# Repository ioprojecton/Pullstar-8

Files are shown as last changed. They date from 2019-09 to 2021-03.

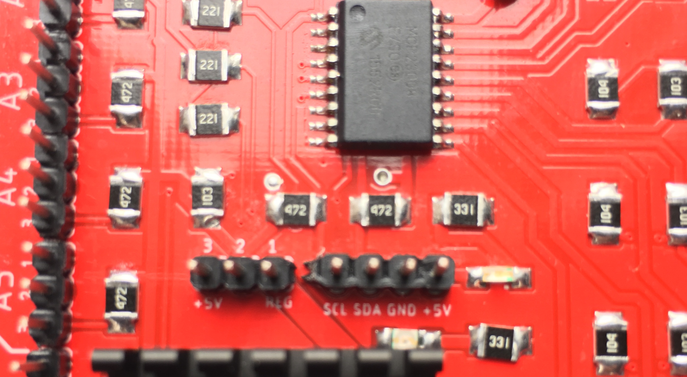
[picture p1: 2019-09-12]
IMG_7.JPG

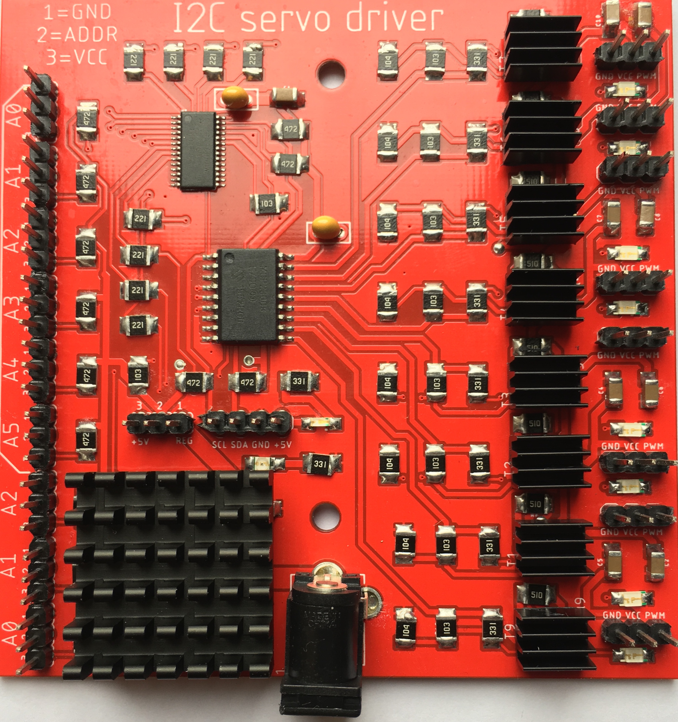
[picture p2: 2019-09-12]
IMG_5.JPG

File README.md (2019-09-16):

# Pullstar-8
I2C 8 Port Servo Driver

The I2C servo driver board by Surepic© is designed to make connecting motors, sensors and other components to your Arduino,Rasberi Pi-based project as fast and easy as possible.

This board allows your Raspberry Pi,Arduino, etc., to control up to 8 servo motors in a simple way via an I2C connection. Thanks to its I2C capabilities, this board saves the Raspberry Pi's,Arduino`s GPIO pins, allowing you to use them for other purposes.

Each of this board's 8 servo motor GPIO pin headers has been spaced out to the standard 3-pin servo pinout (ground, 5V, signal) to make it easier to attach your servo motors and can supply up to 1.25A to each of 8 outputs.

This driver includes headers to connect to a Raspberry Pi,Arduino , so there is no need for soldering to make it up and running.

Using the onboard jumpers for power selection, the input power can be supplied via Arduino's,Rasberi Pi`s regulated voltage, or a completely separate power supply attached to the board's 2.1mm barrel jack. This feature makes this board ideal if you are connecting multiple servos!

Compared to other servo drivers this board offers:
  Independant power control(ON/OFF) to each outputs via i2c.
  Independant duty cycle control to each outputs via i2c.
  Adjustible frequency to up to 1.6khz.
  1.25A per output when powered from external supply.
  LEDs on each output providing feedback if output is ON or OFF.
  2 selectible power sources selectible with jumpers and with led status indicators.
  Onboard voltage regulator (input 6-7v 3A recommended), when barrel jack is used.
  Open collector outputs on power pins.
  I2C addressess are selectable with jumpers for both onboard ics.
  Fully compatible with fast mode I2C 400kbits/s.
  Each board is fully tested before shipping.
  
=========================

Features:

•16 PWM channels, controllable over I2C
•2.1mm industry standard barrel jack port
•Contain an I2C-controlled PWM ic with a built-in clock
•12-bit resolution for each output - for servos(4us at 60hz)
•Controls up to 8 servos
.Dual power inputs (selectible with jumpers).
.Onboard low noise low ripple regulator.
.115 x 105mm size
.Feedback LEDs on each output
.Independant power control to each output

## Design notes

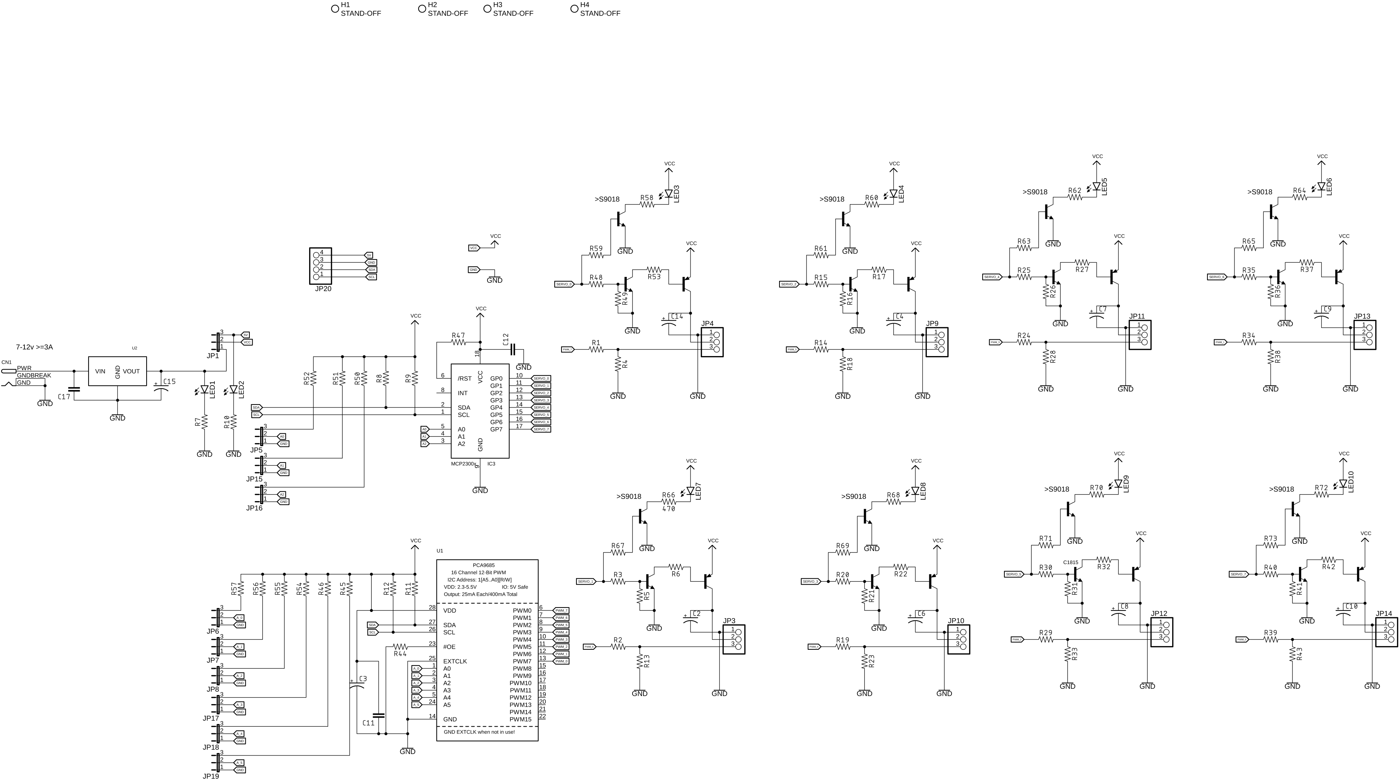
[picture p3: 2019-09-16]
Schematic.jpg

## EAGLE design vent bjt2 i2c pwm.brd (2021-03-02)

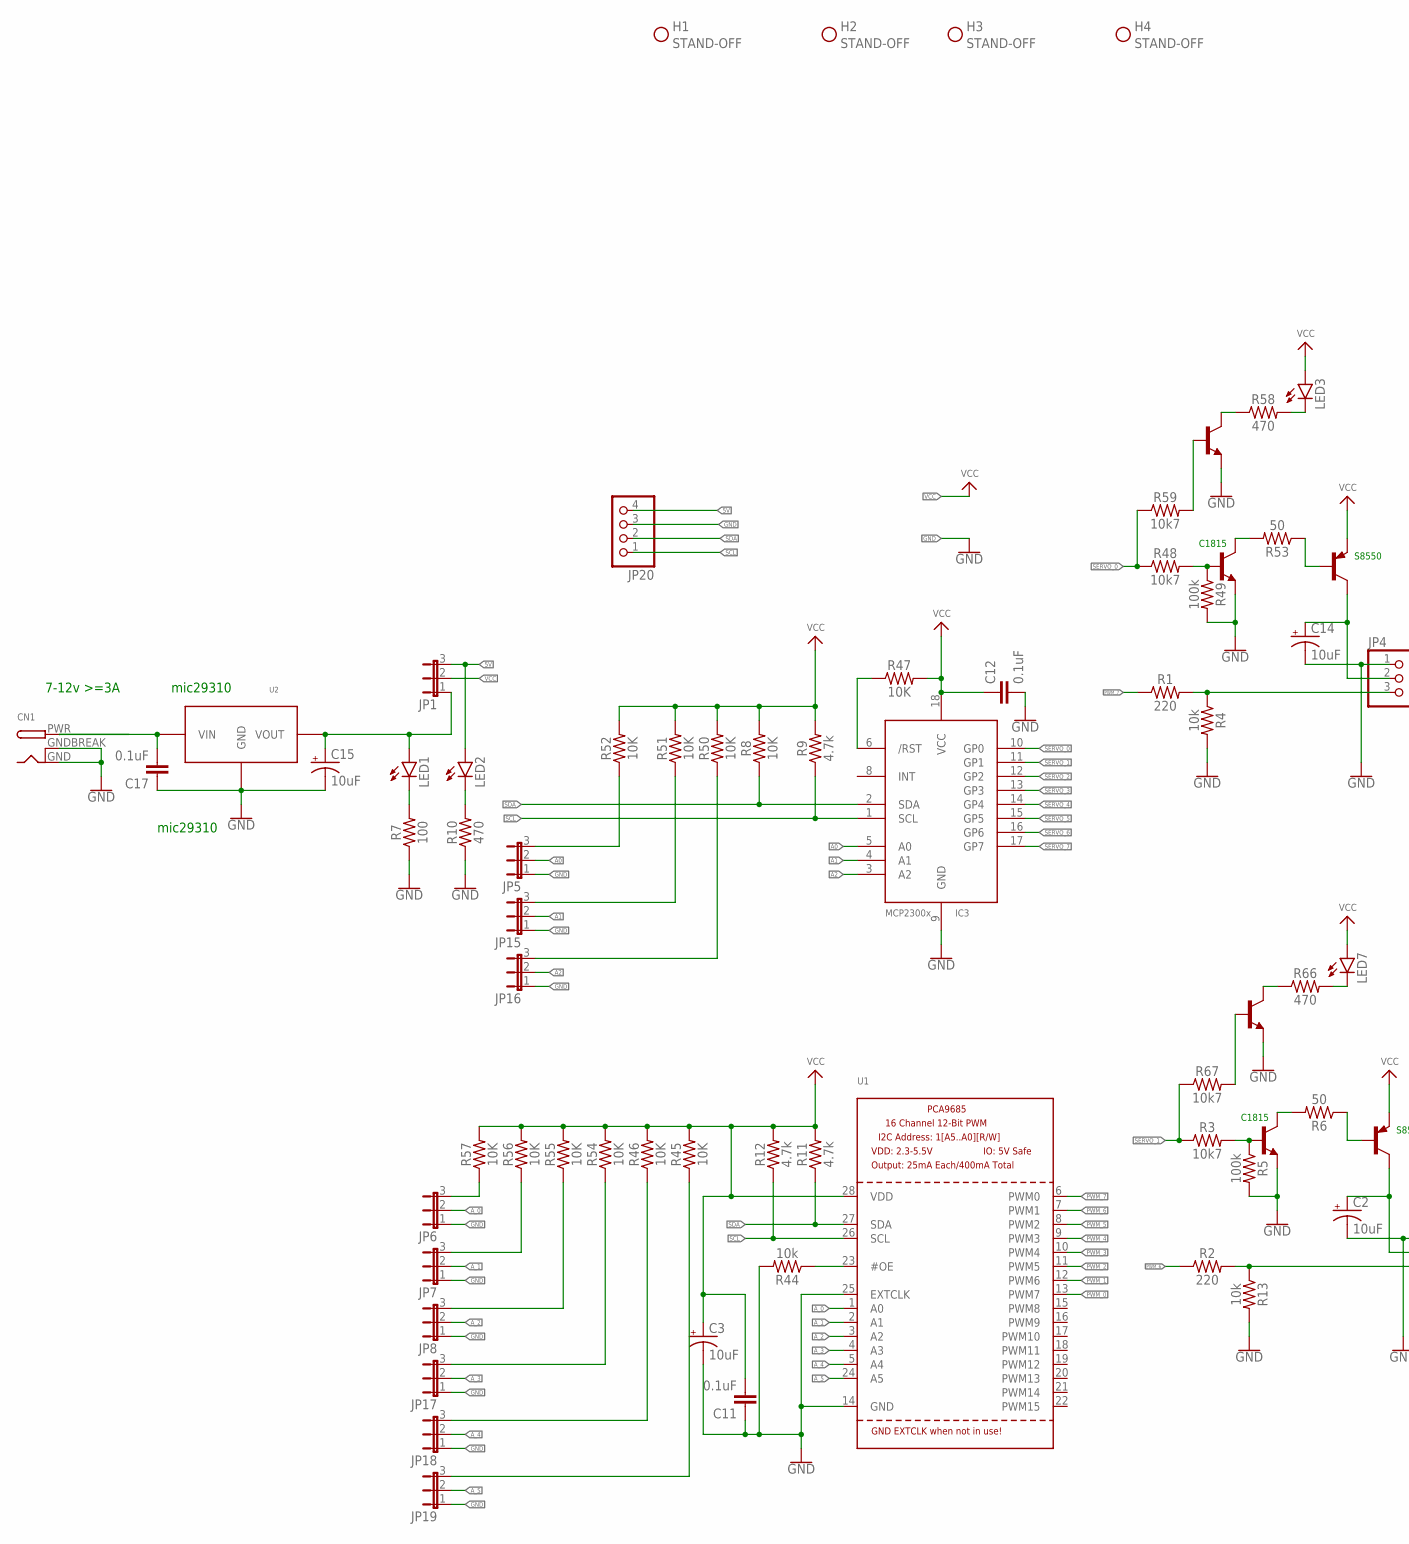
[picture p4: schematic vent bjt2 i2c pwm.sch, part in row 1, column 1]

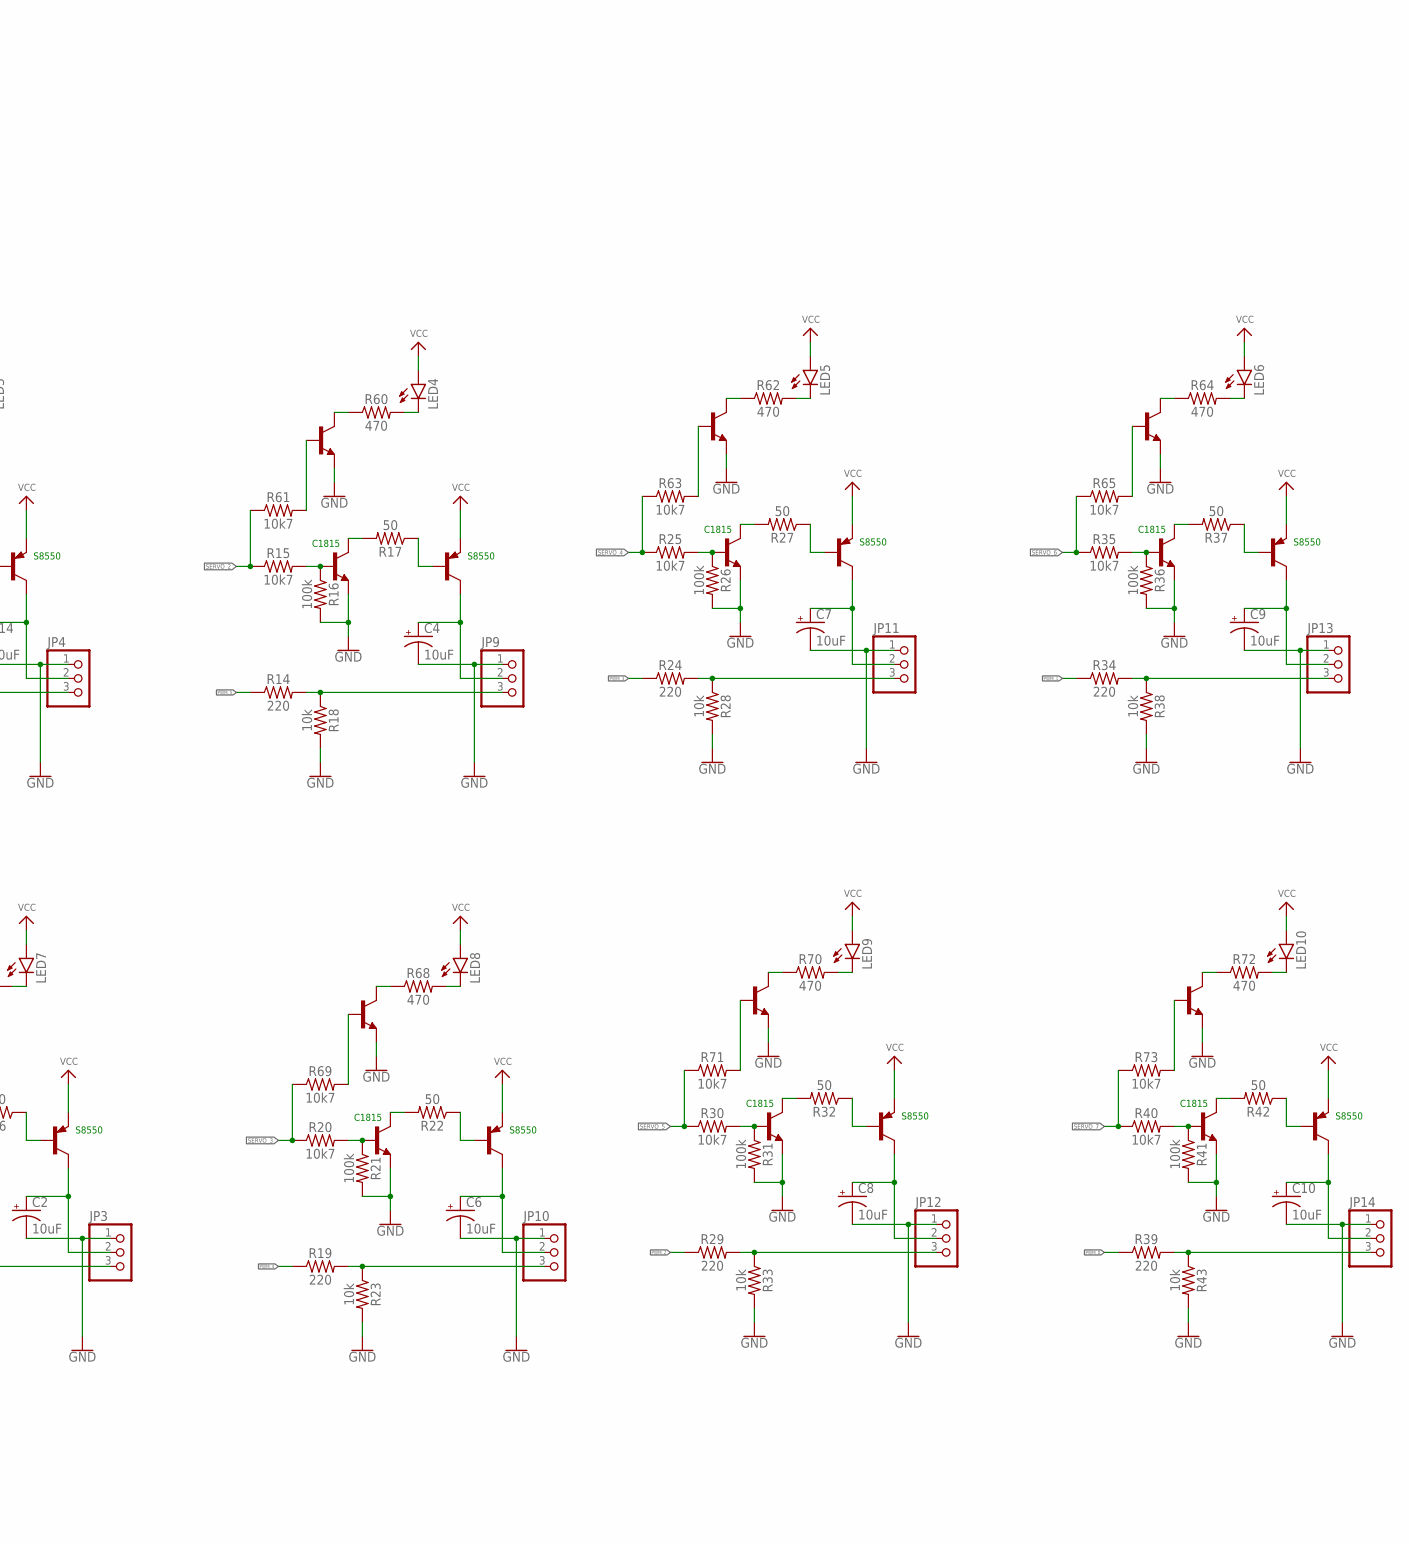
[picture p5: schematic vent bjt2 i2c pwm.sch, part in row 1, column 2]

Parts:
C2, C3, C4, C6, C7, C8, C9, C10, C14, C15: 10uF; CPOL-RADIAL-2.5MM-5MM
C11, C12, C17: 0.1uF; CAP-PTH-SMALL-KIT
CN1: DCBARRELPTH; DCJACK_2MM_PTH
H1, H2, H3, H4: STAND-OFF
IC3: MCP23008/P; DIL18
JP1, JP5, JP6, JP7, JP8, JP15, JP16, JP17, JP18, JP19: JP2E; JP2
JP3, JP4, JP9, JP10, JP11, JP12, JP13, JP14: PINHD-1X3; 1X03
JP20: PINHD-1X4; 1X04
LED1, LED2, LED3, LED4, LED5, LED6, LED7, LED8, LED9, LED10: LEDCHIPLED_1206; CHIPLED_1206
Q1, Q2, Q3, Q4, Q5, Q6, Q7, Q9: 2N2907; TO92-EBC-OVAL
R1, R2, R14, R19, R24, R29, R34, R39: 220; AXIAL-0.3
R3, R15, R20, R25, R30, R35, R40, R48, R59, R61, R63, R65, R67, R69, R71, R73: 10k7; AXIAL-0.3
R4, R13, R18, R23, R28, R33, R38, R43, R44: 10k; AXIAL-0.3
R5, R16, R21, R26, R31, R36, R41, R49: 100k; AXIAL-0.3
R6, R17, R22, R27, R32, R37, R42, R53: 50; AXIAL-0.3
R7: 100; AXIAL-0.3
R8, R45, R46, R47, R50, R51, R52, R54, R55, R56, R57: 10K; AXIAL-0.3
R9, R11, R12: 4.7k; AXIAL-0.3
R10, R58, R60, R62, R64, R66, R68, R70, R72: 470; AXIAL-0.3
T1, T2, T3, T4, T5, T6, T7, T9: 2SC1815; TO92-ECB
U1: PCA9685; TSSOP28
U2: MIC29310_TO-263; TO263-3
U3, U4, U5, U6, U7, U8, U9, U10: S9018; TO92-EBC

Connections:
5V: JP1.3, JP20.4, LED2.A
5V_REG: C15.1 (+), JP1.1, LED1.A, U2.3 (VOUT)
A0: IC3.5 (A0), JP5.2
A1: IC3.4 (A1), JP15.2
A2: IC3.3 (A2), JP16.2
A_0: JP6.2, U1.1 (A0)
A_1: JP7.2, U1.2 (A1)
A_2: JP8.2, U1.3 (A2)
A_3: JP17.2, U1.4 (A3)
A_4: JP18.2, U1.5 (A4)
A_5: JP19.2, U1.24 (A5)
GND: C2.2 (-), C3.2 (-), C4.2 (-), C6.2 (-), C7.2 (-), C8.2 (-), C9.2 (-), C10.2 (-), C11.1, C12.2, C14.2 (-), C15.2 (-), C17.1, CN1.GND, CN1.GNDBREAK, IC3.9 (GND), JP3.1, JP4.1, JP5.1, JP6.1, JP7.1, JP8.1, JP9.1, JP10.1, JP11.1, JP12.1, JP13.1, JP14.1, JP15.1, JP16.1, JP17.1, JP18.1, JP19.1, JP20.3, R4.P$2 (2), R5.P$2 (2), R7.P$1 (1), R10.P$1 (1), R13.P$2 (2), R16.P$2 (2), R18.P$2 (2), R21.P$2 (2), R23.P$2 (2), R26.P$2 (2), R28.P$2 (2), R31.P$2 (2), R33.P$2 (2), R36.P$2 (2), R38.P$2 (2), R41.P$2 (2), R43.P$2 (2), R44.P$2 (2), R49.P$2 (2), T1.E, T2.E, T3.E, T4.E, T5.E, T6.E, T7.E, T9.E, U1.14 (GND), U1.25 (EXTCLK), U2.2 (GND), U2.TAB (GND), U3.E, U4.E, U5.E, U6.E, U7.E, U8.E, U9.E, U10.E
unnamed: JP4.3, R1.P$2 (2), R4.P$1 (1)
unnamed: JP3.3, R2.P$2 (2), R13.P$1 (1)
unnamed: Q9.B, R53.P$1 (1)
unnamed: R3.P$2 (2), R5.P$1 (1), T1.B
unnamed: R6.P$2 (2), T1.C
unnamed: JP8.3, R55.P$1 (1)
unnamed: C2.1 (+), JP3.2, Q1.C
unnamed: C17.2, CN1.PWR, U2.1 (VIN)
unnamed: Q1.B, R6.P$1 (1)
unnamed: JP9.3, R14.P$2 (2), R18.P$1 (1)
unnamed: JP6.3, R57.P$1 (1)
unnamed: JP7.3, R56.P$1 (1)
unnamed: R44.P$1 (1), U1.23 (#OE)
unnamed: LED1.C, R7.P$2 (2)
unnamed: LED2.C, R10.P$2 (2)
unnamed: R58.P$1 (1), U3.C
unnamed: JP17.3, R54.P$1 (1)
unnamed: JP18.3, R46.P$1 (1)
unnamed: R15.P$2 (2), R16.P$1 (1), T2.B
unnamed: R17.P$2 (2), T2.C
unnamed: C4.1 (+), JP9.2, Q2.C
unnamed: Q2.B, R17.P$1 (1)
unnamed: JP10.3, R19.P$2 (2), R23.P$1 (1)
unnamed: R20.P$2 (2), R21.P$1 (1), T3.B
unnamed: R22.P$2 (2), T3.C
unnamed: C6.1 (+), JP10.2, Q3.C
unnamed: Q3.B, R22.P$1 (1)
unnamed: JP11.3, R24.P$2 (2), R28.P$1 (1)
unnamed: R25.P$2 (2), R26.P$1 (1), T4.B
unnamed: R27.P$2 (2), T4.C
unnamed: C7.1 (+), JP11.2, Q4.C
unnamed: Q4.B, R27.P$1 (1)
unnamed: JP12.3, R29.P$2 (2), R33.P$1 (1)
unnamed: R30.P$2 (2), R31.P$1 (1), T5.B
unnamed: R32.P$2 (2), T5.C
unnamed: C8.1 (+), JP12.2, Q5.C
unnamed: Q5.B, R32.P$1 (1)
unnamed: JP13.3, R34.P$2 (2), R38.P$1 (1)
unnamed: R35.P$2 (2), R36.P$1 (1), T6.B
unnamed: R37.P$2 (2), T6.C
unnamed: C9.1 (+), JP13.2, Q6.C
unnamed: Q6.B, R37.P$1 (1)
unnamed: JP19.3, R45.P$1 (1)
unnamed: JP5.3, R52.P$1 (1)
unnamed: JP15.3, R51.P$1 (1)
unnamed: JP16.3, R50.P$1 (1)
unnamed: IC3.6 (/RST), R47.P$1 (1)
unnamed: JP14.3, R39.P$2 (2), R43.P$1 (1)
unnamed: R48.P$2 (2), R49.P$1 (1), T9.B
unnamed: R53.P$2 (2), T9.C
unnamed: R40.P$2 (2), R41.P$1 (1), T7.B
unnamed: C14.1 (+), JP4.2, Q9.C
unnamed: R42.P$2 (2), T7.C
unnamed: C10.1 (+), JP14.2, Q7.C
unnamed: Q7.B, R42.P$1 (1)
unnamed: LED3.C, R58.P$2 (2)
unnamed: R59.P$2 (2), U3.B
unnamed: R60.P$1 (1), U4.C
unnamed: LED4.C, R60.P$2 (2)
unnamed: R61.P$2 (2), U4.B
unnamed: R62.P$1 (1), U5.C
unnamed: LED5.C, R62.P$2 (2)
unnamed: R63.P$2 (2), U5.B
unnamed: R64.P$1 (1), U6.C
unnamed: LED6.C, R64.P$2 (2)
unnamed: R65.P$2 (2), U6.B
unnamed: R66.P$1 (1), U7.C
unnamed: LED7.C, R66.P$2 (2)
unnamed: R67.P$2 (2), U7.B
unnamed: R68.P$1 (1), U8.C
unnamed: LED8.C, R68.P$2 (2)
unnamed: R69.P$2 (2), U8.B
unnamed: R70.P$1 (1), U9.C
unnamed: LED9.C, R70.P$2 (2)
unnamed: R71.P$2 (2), U9.B
unnamed: R72.P$1 (1), U10.C
unnamed: LED10.C, R72.P$2 (2)
unnamed: R73.P$2 (2), U10.B
PWM_0: R39.P$1 (1), U1.13 (PWM7)
PWM_1: R34.P$1 (1), U1.12 (PWM6)
PWM_2: R29.P$1 (1), U1.11 (PWM5)
PWM_3: R24.P$1 (1), U1.10 (PWM4)
PWM_4: R19.P$1 (1), U1.9 (PWM3)
PWM_5: R14.P$1 (1), U1.8 (PWM2)
PWM_6: R2.P$1 (1), U1.7 (PWM1)
PWM_7: R1.P$1 (1), U1.6 (PWM0)
SCL: IC3.1 (SCL), JP20.1, R9.P$1 (1), R12.P$1 (1), U1.26 (SCL)
SDA: IC3.2 (SDA), JP20.2, R8.P$1 (1), R11.P$1 (1), U1.27 (SDA)
SERVO_0: IC3.10 (GP0), R48.P$1 (1), R59.P$1 (1)
SERVO_1: IC3.11 (GP1), R3.P$1 (1), R67.P$1 (1)
SERVO_2: IC3.12 (GP2), R15.P$1 (1), R61.P$1 (1)
SERVO_3: IC3.13 (GP3), R20.P$1 (1), R69.P$1 (1)
SERVO_4: IC3.14 (GP4), R25.P$1 (1), R63.P$1 (1)
SERVO_5: IC3.15 (GP5), R30.P$1 (1), R71.P$1 (1)
SERVO_6: IC3.16 (GP6), R35.P$1 (1), R65.P$1 (1)
SERVO_7: IC3.17 (GP7), R40.P$1 (1), R73.P$1 (1)
VCC: C3.1 (+), C11.2, C12.1, IC3.18 (VCC), JP1.2, LED3.A, LED4.A, LED5.A, LED6.A, LED7.A, LED8.A, LED9.A, LED10.A, Q1.E, Q2.E, Q3.E, Q4.E, Q5.E, Q6.E, Q7.E, Q9.E, R8.P$2 (2), R9.P$2 (2), R11.P$2 (2), R12.P$2 (2), R45.P$2 (2), R46.P$2 (2), R47.P$2 (2), R50.P$2 (2), R51.P$2 (2), R52.P$2 (2), R54.P$2 (2), R55.P$2 (2), R56.P$2 (2), R57.P$2 (2), U1.28 (VDD)

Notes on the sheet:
7-12v >=3A
C1815
S8550
mic29310

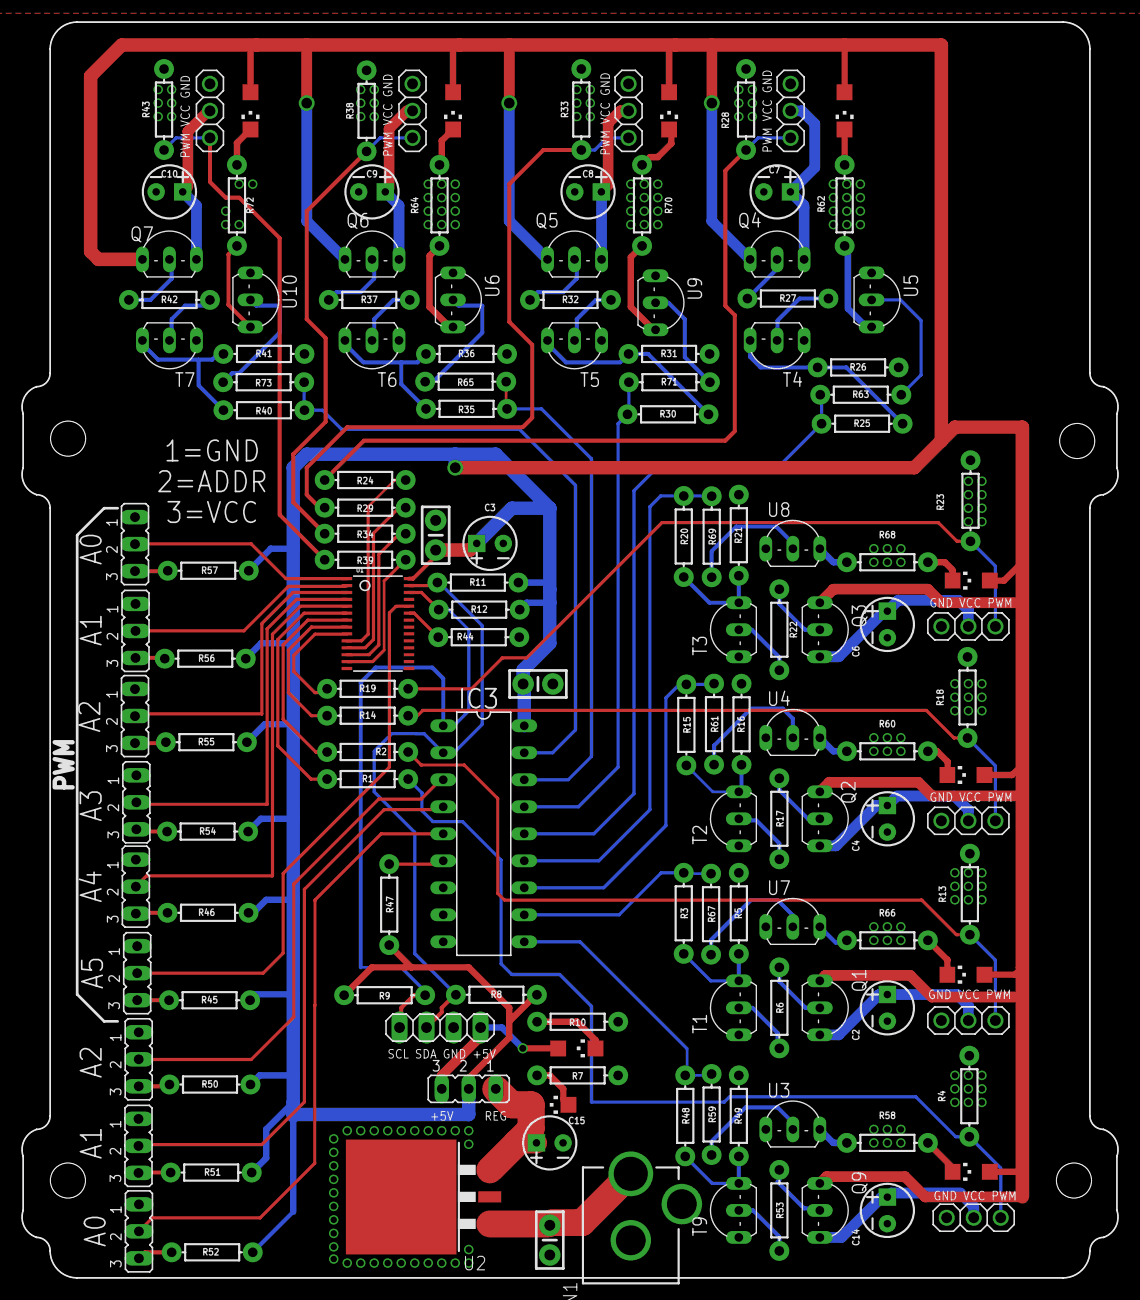
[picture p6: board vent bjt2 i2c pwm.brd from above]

Board: 2 copper layers, 103.1 x 118.1 mm, 147 parts (0 on the bottom side), 109 nets.

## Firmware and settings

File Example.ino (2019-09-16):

#include <Wire.h>
//#include "PCA9685.h"
#define mcp_ic_address 0
#define ON 1
#define OFF 0
//#define wait_time 4

bool mcp_ic_initialize(unsigned char);
bool mcp_ic_port(unsigned char address, unsigned char port, bool value);

PCA9685 pwmController(Wire, PCA9685_PhaseBalancer_Weaved);

PCA9685_ServoEvaluator pwmServo1(150, 324, 500);

void setup() {
  while (!mcp_ic_initialize(mcp_ic_address));
  pwmController.init(B000000);
  pwmController.setPWMFrequency(50);


}

void loop() {

  mcp_ic_port(mcp_ic_address, 1, ON);

  pwmController.setChannelPWM(0, pwmServo1.pwmForAngle(90));

  pwmController.setChannelPWM(0, pwmServo1.pwmForAngle(0));

  pwmController.setChannelPWM(0, pwmServo1.pwmForAngle(-90));

  mcp_ic_port(mcp_ic_address, 0, OFF);

}

bool mcp_ic_initialize(unsigned char _address) {
#define IODIR 0x00
#define IOCON 0x05
#define mcp_address 0x20


  if (mcp_address + _address > 0x2F) return 0;

  Wire.begin();
  //Wire.setClock(400000);
  Wire.beginTransmission(mcp_address + _address);
  Wire.write(IODIR);
  Wire.write(0x00);
  Wire.endTransmission();

  Wire.beginTransmission(mcp_address + _address);
  Wire.write(IOCON);
  Wire.write(0x020);
  Wire.endTransmission();

  return 1;
}

bool mcp_ic_port(unsigned char address, unsigned char port, bool value) {
#define OLAT 0x0A
#ifndef mcp_address
#define mcp_address 0x20
#endif

  if ((mcp_address + address > 0x2F) || (port > 7)) return 0;

  Wire.beginTransmission(mcp_address + address);

  Wire.write(OLAT);

  static unsigned char gpio;

  if (value) gpio |= (value << port);

  if (!value) gpio ^= (!value << port);

  Wire.write(gpio);
  Wire.endTransmission();


  return 1;
}

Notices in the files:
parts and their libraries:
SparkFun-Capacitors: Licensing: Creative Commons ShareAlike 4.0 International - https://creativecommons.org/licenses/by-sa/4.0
